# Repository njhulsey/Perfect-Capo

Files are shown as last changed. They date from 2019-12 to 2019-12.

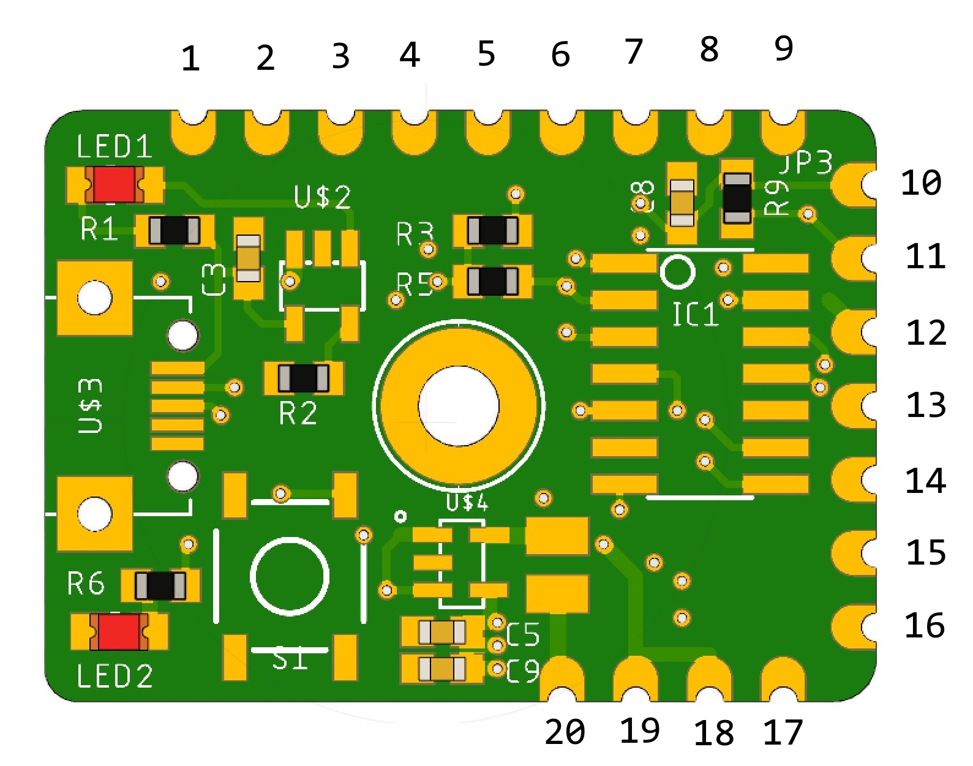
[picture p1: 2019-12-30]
Photos/pinout.jpg

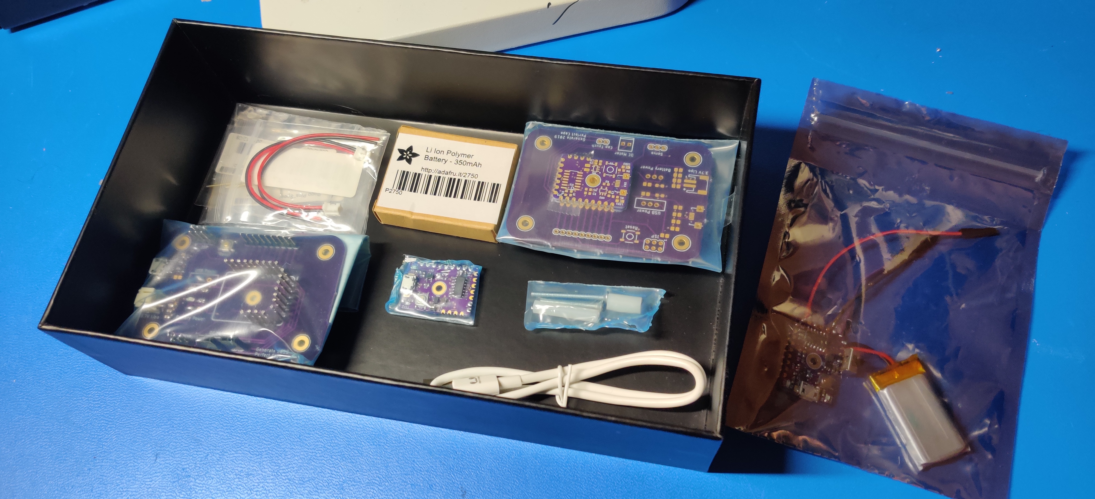
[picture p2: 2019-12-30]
Photos/IMG_20191204_212945.jpg

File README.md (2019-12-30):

# Perfect-Capo
The electrical system of perfect-capo is capable of unclenching the clamp mechanism via capacitive touch. The board uses an ATtiny84 MCU for basic logic and control. It is capable of driving the speed and direction of a DC Motor via an H-bridge. The pins along the edge of the PCB are for external connections to be soldered on (such as Motor, Capacitive touch, Battery, Switch). The entire system is powered by a 3.7v LiPo Battery which is buck-boosted to 5v for better motor performance. A Micro-USB connector is present for programming and battery charging. The MCU uses a bootloader to simulate USB for simple hardware implementation. It is also able to charge the LiPo via the MCP73831 IC. Many additional pinouts are available for easy hackability and ease of use.

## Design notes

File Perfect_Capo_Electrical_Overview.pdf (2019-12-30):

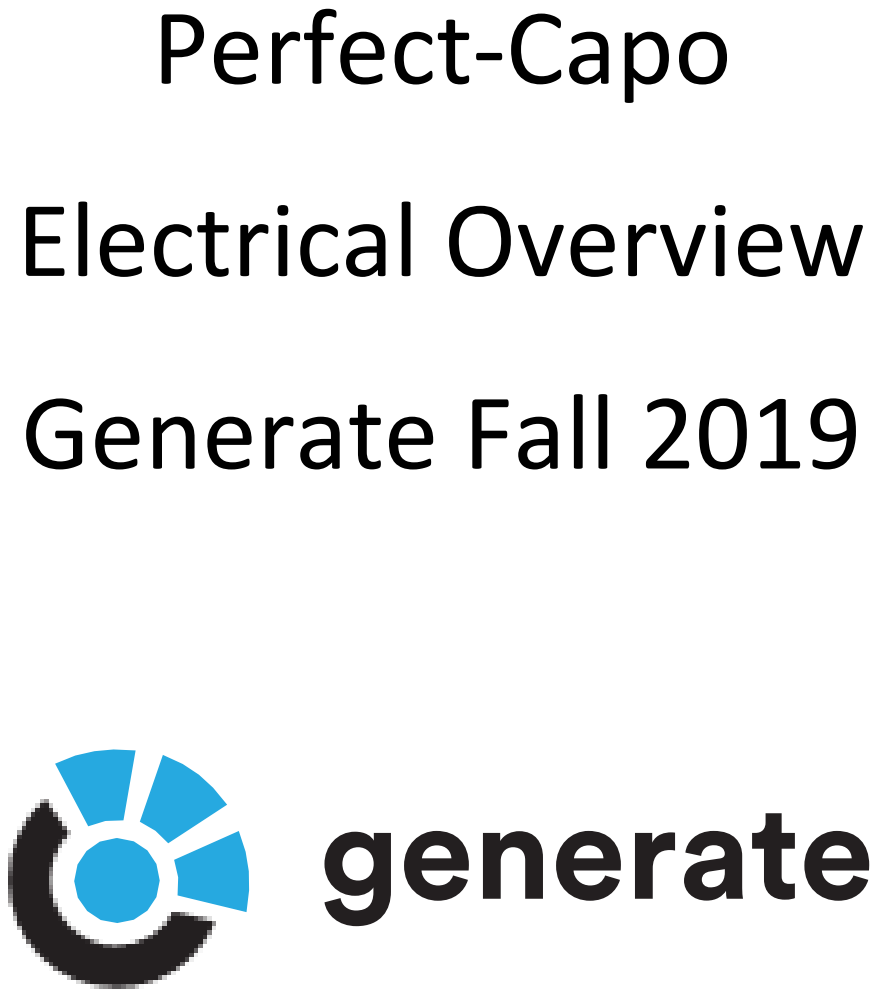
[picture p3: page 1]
Perfect-Capo; Electrical Overview; Generate Fall 2019

## Overview:

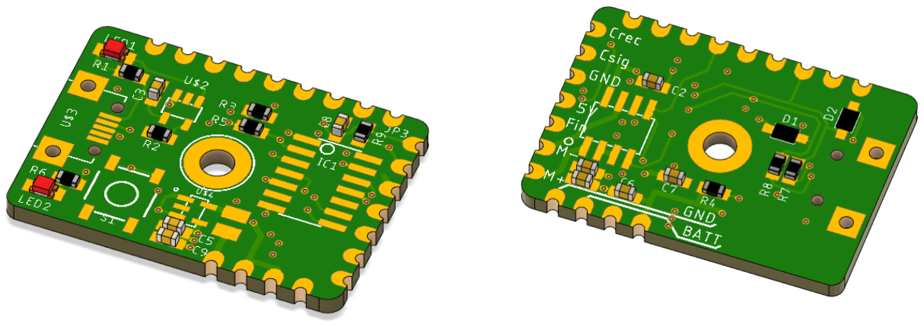
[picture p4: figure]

The electrical system of perfect-capo is capable of unclenching the clamp mechanism via capacitive touch. The board uses an ATtiny84 MCU for basic logic and control. It is capable of driving the speed and direction of a DC Motor via an H-bridge. The pins along the edge of the PCB are for external connections to be soldered on (such as Motor, Capacitive touch, Battery, Switch). The entire system is powered by a 3.7v LiPo Battery which is buck-boosted to 5v for better motor performance. A Micro-USB connector is present for programming and battery charging. The MCU uses a bootloader to simulate USB for simple hardware implementation. It is also able to charge the LiPo via the MCP73831 IC. Many additional pinouts are available for easy hackability and ease of use.

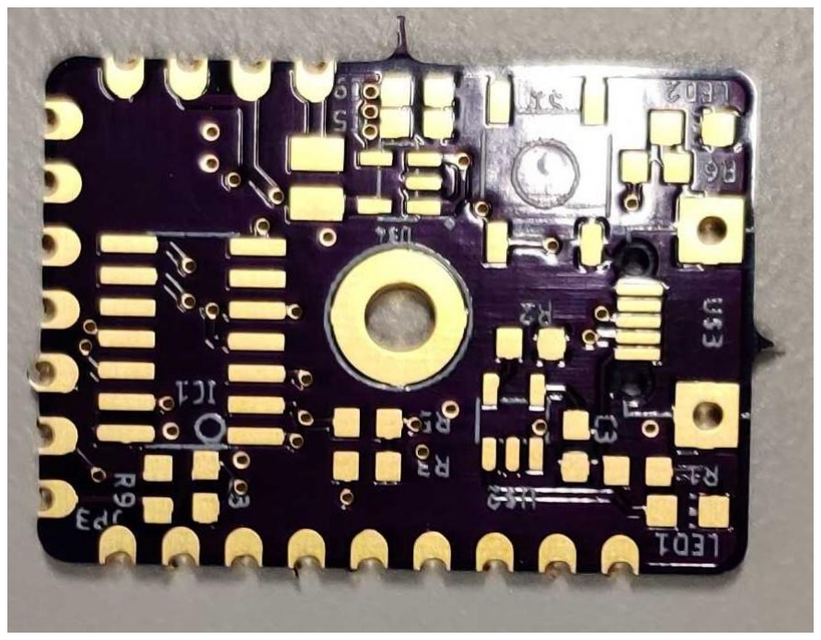
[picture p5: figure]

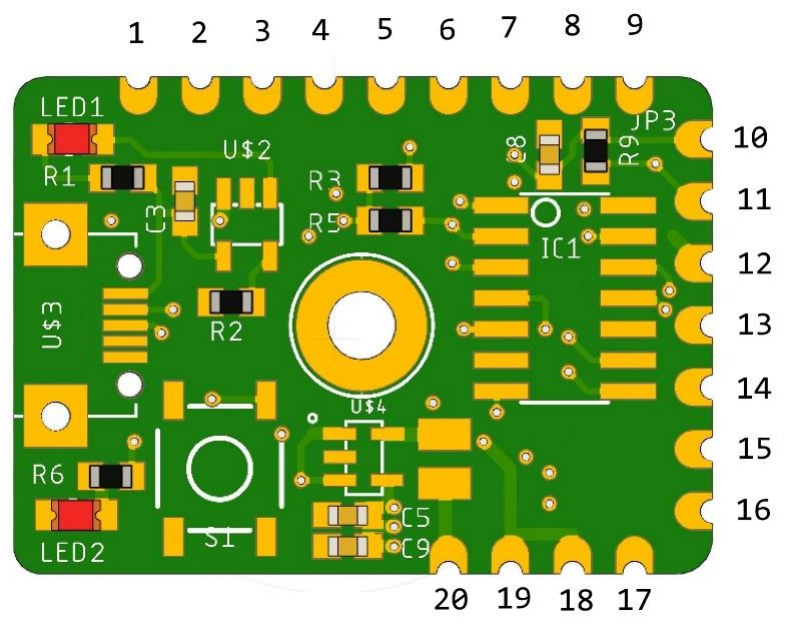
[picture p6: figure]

Pin | Function | Pin_Ref
1 | Miso | 5
2 | Reset | Reset(11)
3 | D- | 10
4 | D+ | 9
5 | GND | GND
6 | Rin | 6
7 | Fin | 8
8 | SCK | 4
9 | 5V | 5V
10 | Cap_Rec | 2
11 | Cap_Sig | 1
12 | GND | GND
13 | 5V | 5v
14 | Fin | 8
15 | M- | N/A
16 | M+ | N/A
17 | Bat_GND | N/A
18 | V_Bat | N/A
19 | Switch1 | N/A
20 | Switch2 | N/A

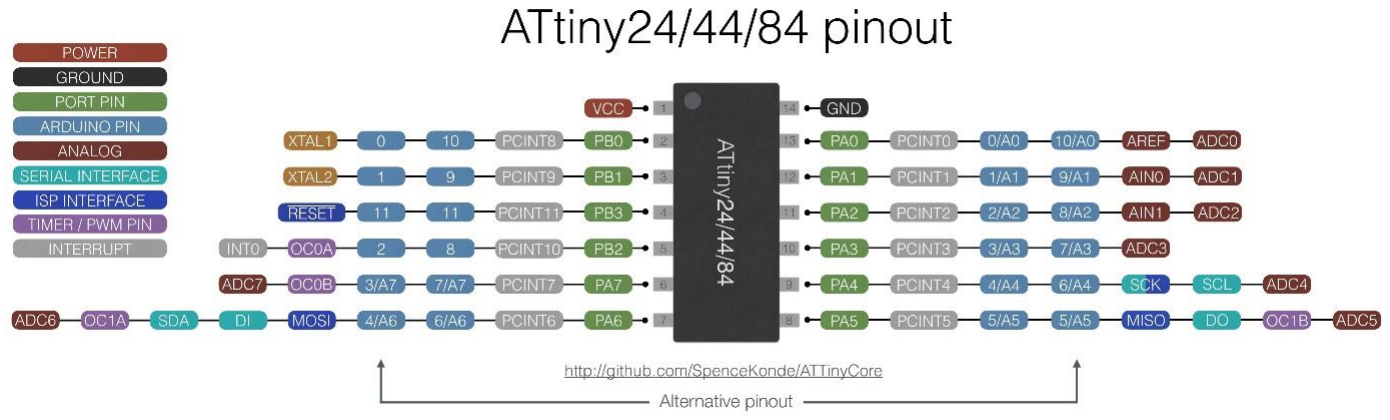
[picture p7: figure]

## Hardware:

The hardware overview will focus on each crucial portion of the schematic. Explaining how it works, its limits, why its there, and additional information.

Sections:

- ATtiny 84
- 5V Booster
- H-Bridge
- LiPo Charger

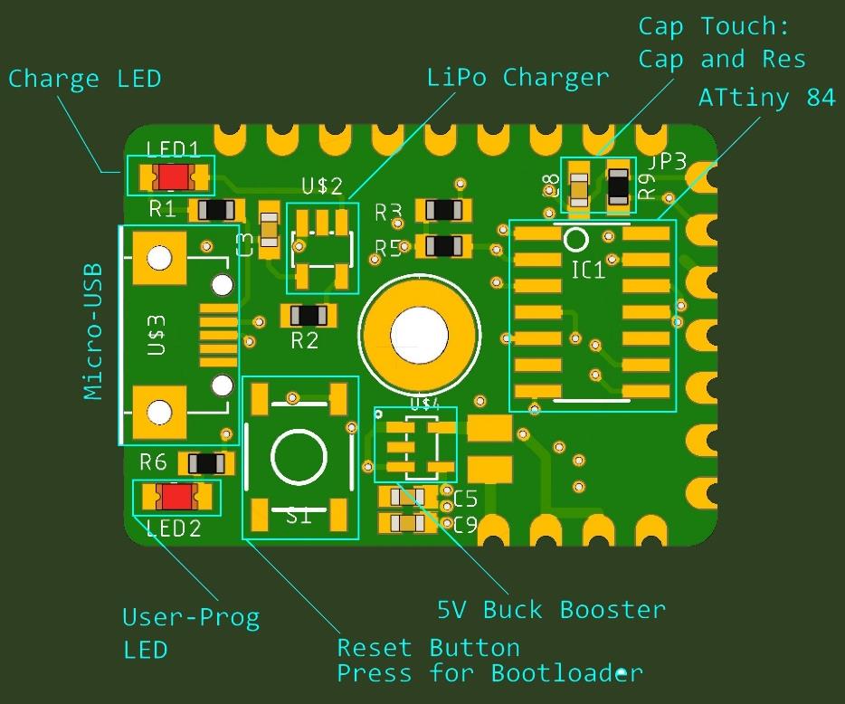
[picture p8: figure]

Physical Board Layout

## ATtiny 84:

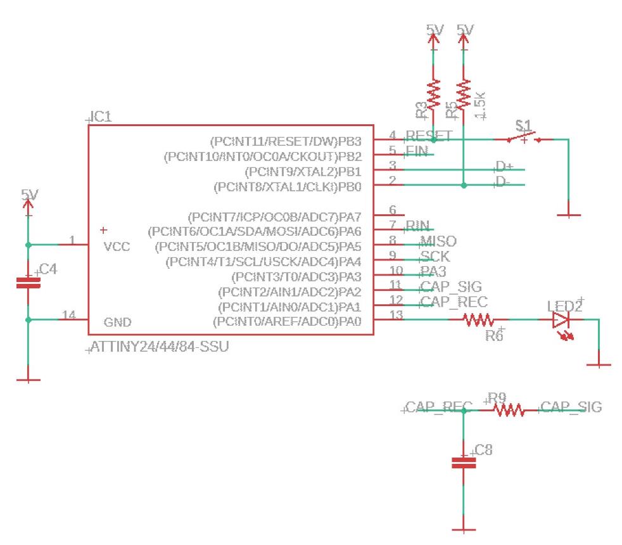
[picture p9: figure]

The ATtiny84 holds the core functionality and logic for the device. It engages the motor as it detects the capacitive touch. There is a debug LED used for testing purposes or additional indication. The Reset button is required to force the ATtiny84 into it’s bootloader. Once in the bootloader the device will wait for 10 seconds before running the user defined program. During those 10 seconds the user defined program can be rewritten with IDE and Micro-USB. C8 and R9 are used for setting the RC constant for capacitive touch (more info in software section). As usual there is a 100nF capacitor near the 5V and GND pin to reduce noise.

Additional Resources:

- Bootloader How-To:
- https://learn.sparkfun.com/tutorials/how-to-install-an-attiny-bootloader-with-virtualusb/all (https://learn.sparkfun.com/tutorials/how-to-install-an-attiny-bootloader-with-virtual-usb/all)
- Capacitive Touch:
- https://playground.arduino.cc/Main/CapacitiveSensor/
- ATtiny 84:
- https://www.digikey.com/product-detail/en/microchip-technology/ATTINY84A-SSUR/ATTINY84A-SSURCT-ND/2774136 (https://www.digikey.com/product-detail/en/microchip-technology/ATTINY84A-SSUR/ATTINY84A-SSURCT-ND/2774136)

## 5V Buck-Booster:

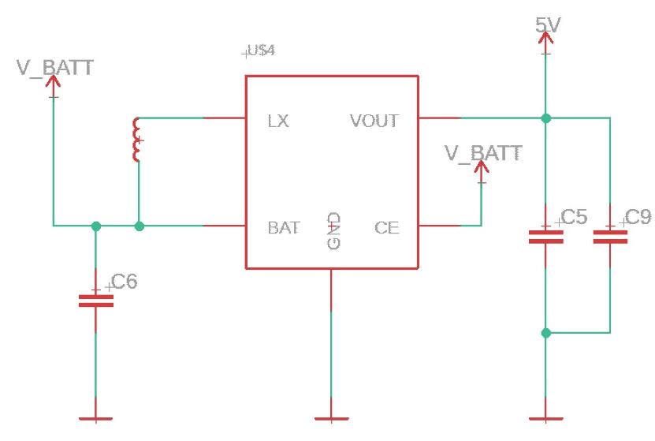
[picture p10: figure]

The XC9141B50 IC is capable of boosting the LiPo battery and providing 5V and 800mA to the entire system. It uses a 4.7uH inductor with a switching frequency of 1Mhz. It provides just enough to power the DC motor. Ideally it should be able to supply more current since the max torque current draw of the DC Motor is exactly 800mA. Also, more capacitance is needed. Additional capacitors were soldered on after fabrication. The capacitors used here were rated: 0603 10V 10uF.

Additional Resources:

- Buck Booster IC:
- https://www.digikey.com/product-detail/en/torex-semiconductor-ltd/XC9141B50CMR-G/893-1369-1-ND/6148753 (https://www.digikey.com/product-detail/en/torex-semiconductor-ltd/XC9141B50CMR-G/893-1369-1-ND/6148753)
- Inductor:
- https://www.digikey.com/product-detail/en/w-rth-elektronik/74405024047/732-10778-1-ND/6598212 (https://www.digikey.com/product-detail/en/w-rth-elektronik/74405024047/732-10778-1-ND/6598212)

## H-Bridge:

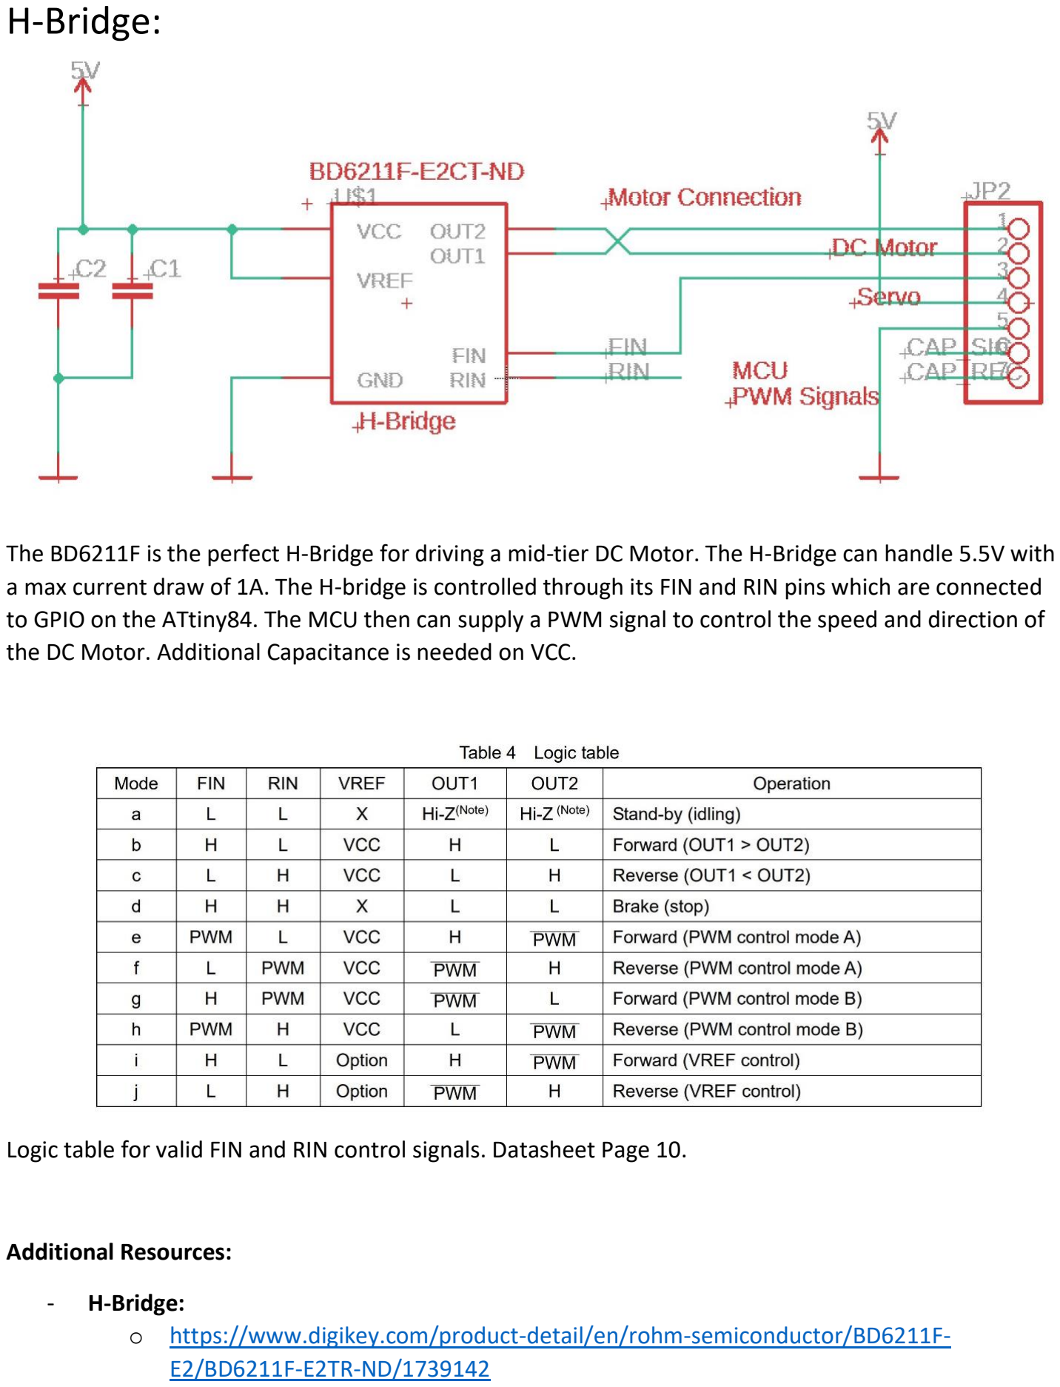
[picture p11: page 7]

The BD6211F is the perfect H-Bridge for driving a mid-tier DC Motor. The H-Bridge can handle 5.5V with a max current draw of 1A. The H-bridge is controlled through its FIN and RIN pins which are connected to GPIO on the ATtiny84. The MCU then can supply a PWM signal to control the speed and direction of the DC Motor. Additional Capacitance is needed on VCC.

Logic table for valid FIN and RIN control signals. Datasheet Page 10.

Additional Resources:

- H-Bridge:
- https://www.digikey.com/product-detail/en/rohm-semiconductor/BD6211F-E2/BD6211F-E2TR-ND/1739142 (https://www.digikey.com/product-detail/en/rohm-semiconductor/BD6211F-E2/BD6211F-E2TR-ND/1739142)

## Lipo-Charger:

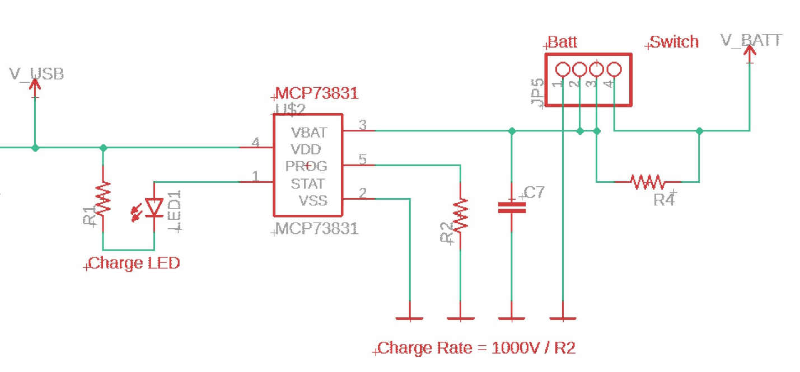
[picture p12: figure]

The MCP73831 is an amazingly convenient single cell 4.2v LiPo charger. It’s easy to implement and operate. A single resistor sets the charge rate (which should not be greater than the capacity of the LiPo). The LED indicates the charge status. The STAT pin will be grounded while charging and high when done charging. The direction of the LED will indicate either state.

It should be noted that the photo above also includes pinouts (JP5:3 JP5:4) for a switch (which is also R4). This could be used as a power switch for the perfect-capo unit.

Additional Resources:

- LiPo Charger IC:
- https://www.digikey.com/product-detail/en/MCP73831T-2ACI%2fOT/MCP73831T-2ACI%2fOTCT-ND/1979802 (https://www.digikey.com/product-detail/en/MCP73831T-2ACI%2fOT/MCP73831T-2ACI%2fOTCT-ND/1979802)

## Development Board:

Since the Perfect-Capo PCB is rather small, a development board was created to help with initial prototyping and ease of interfacing. Another use for the development board could be for mass production testing. The board has pogo-pins which allow for quick and easy temporary connection. The dev board can perform initial programming and testing before continuing through production.

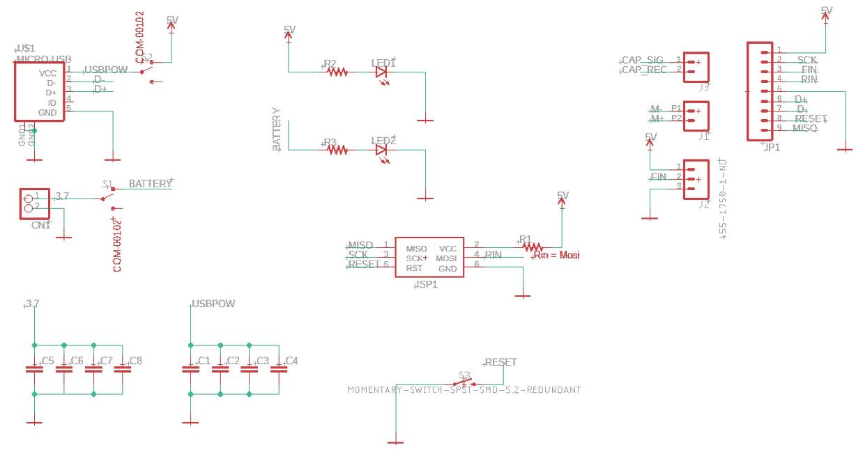
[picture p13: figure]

The Development Board provides a connector for every feature of the perfect-capo PCB. The PCB has power switches for Battery and USB which allows for power selection. Pin headers are primarily used for external connections. There is also ISP Programming pins for initial bootloader flashing. Silkscreen also provides information, labelling each connector.

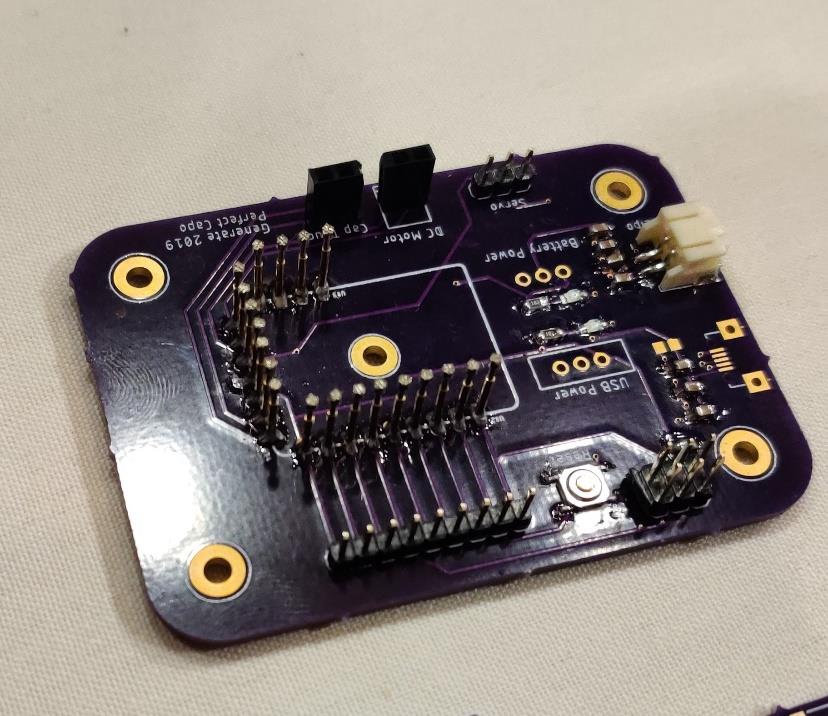
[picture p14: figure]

## What’s in The Box?

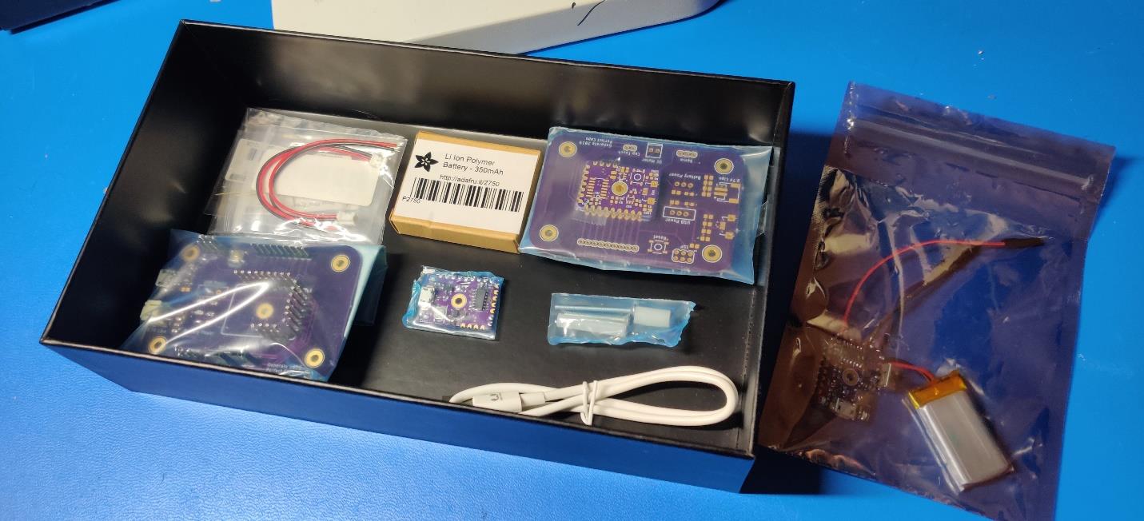
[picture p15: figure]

The box handed off to the client will contain the entire electrical prototype as well as spare electrical components crucial to development.

Contents:

- Capo electrical prototype
- 1x PCBA Dev board and capo controller
- Spare Battery
- Micro-Usb cable
- Spare Hardware
- Spare Battery connectors and pogo pins
- 2x PCB Dev board and capo controller

## BOM

Part Number | Description | Price | Quantity
CDS0D323-T08L | USB TVS Diode | $0.73 | 2
TL3342F160QG | Reset Button! | $0.70 | 1
ATTINY84A-SSUR | MCU | $0.84 | 1
MCP73831T-2ACI/OT | USB Charger | $0.58 | 1
10118194-0001LF | Micro USB | $0.43 | 1
1528-1858-ND | Battery 350mAh | $6.95 | 1
587-3258-1-ND | 0603 10uF 10V Cap | $0.19 | 35
XC9141B50CMR-G | IC REG BOOST 5V 800MA SOT25 | $1.27 | 1
732-10778-1-ND | FIXED IND 4.7UH 1A 270 MOHM MAX | $0.63 | 1
Various Resistors not shown

## Additional Photos:

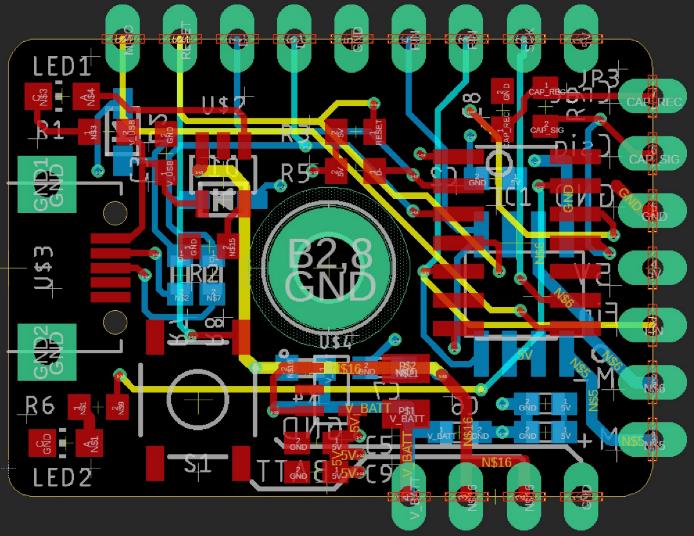
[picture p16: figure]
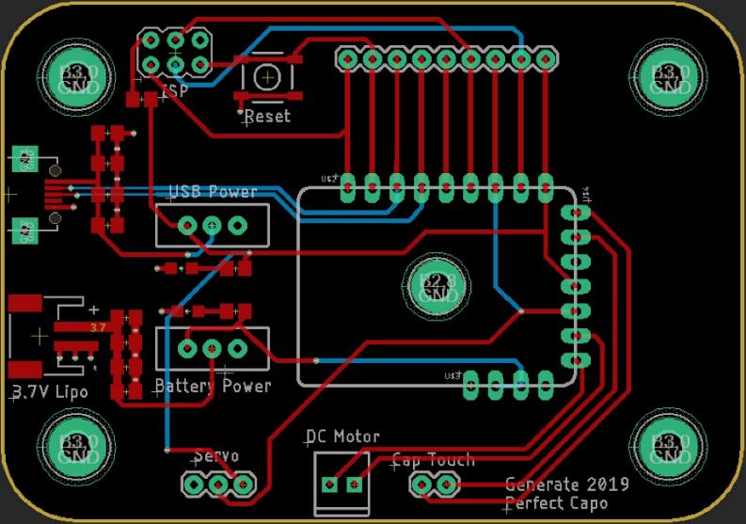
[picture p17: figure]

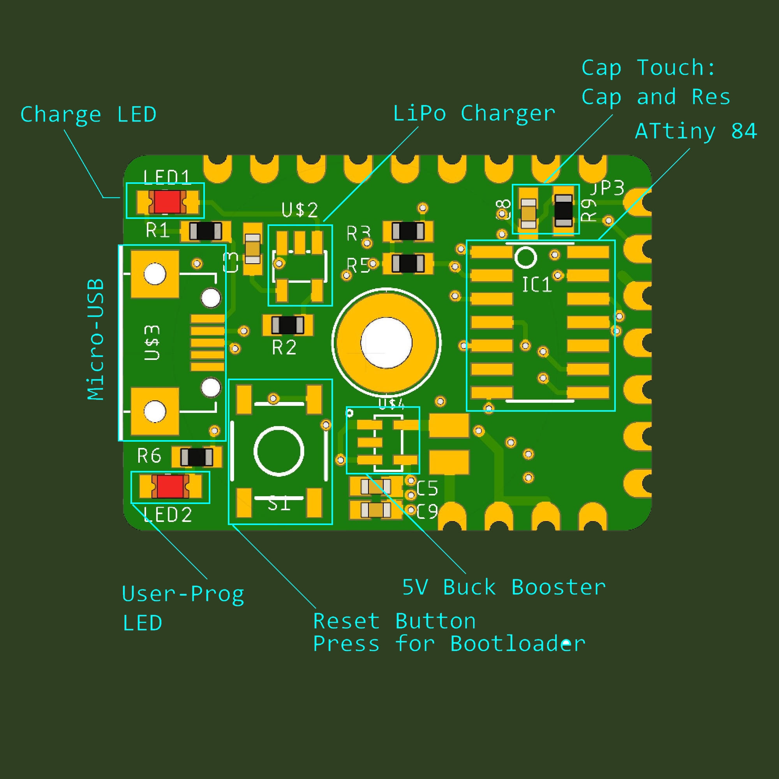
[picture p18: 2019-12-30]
Photos/HardWare.jpg

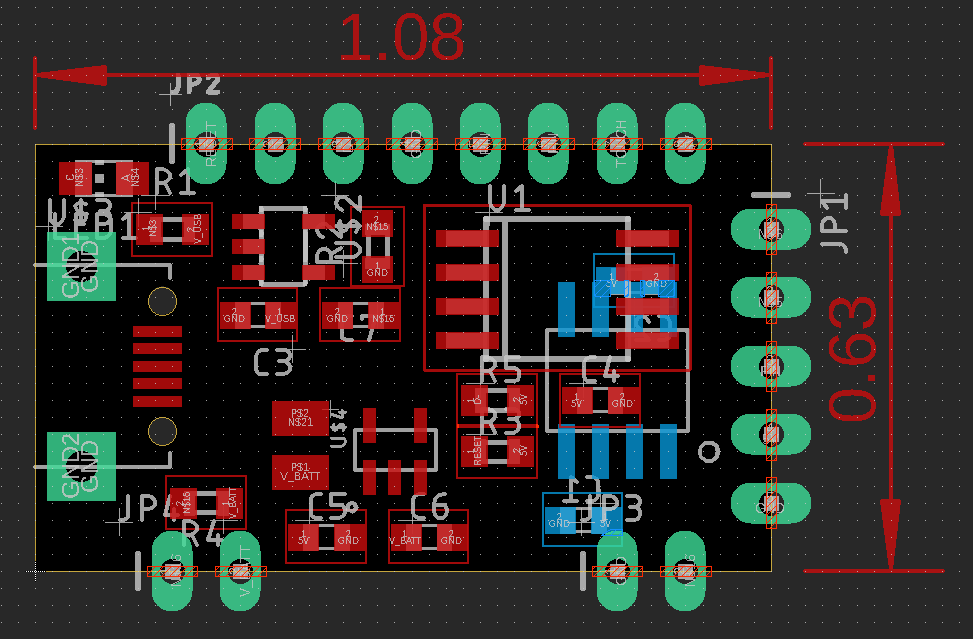
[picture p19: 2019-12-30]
Eagle_Files/Initial_Board.PNG

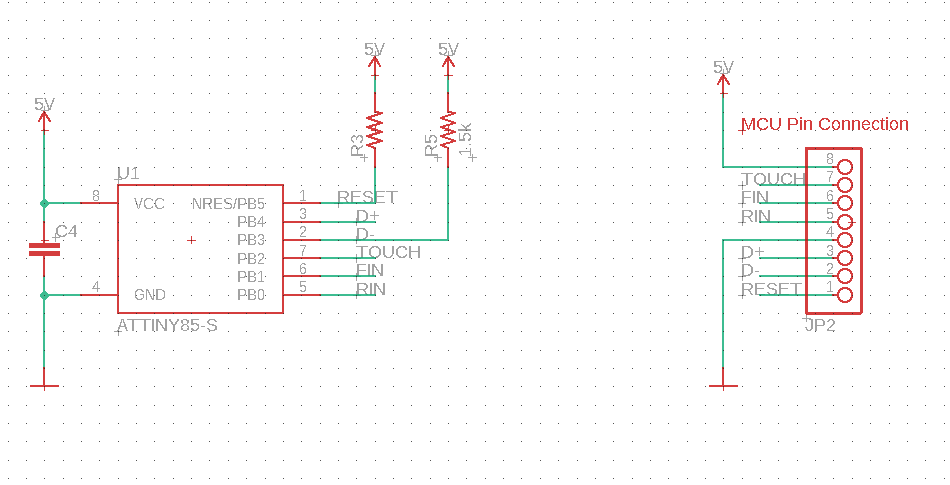
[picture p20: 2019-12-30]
Eagle_Files/MCU-Pins.PNG

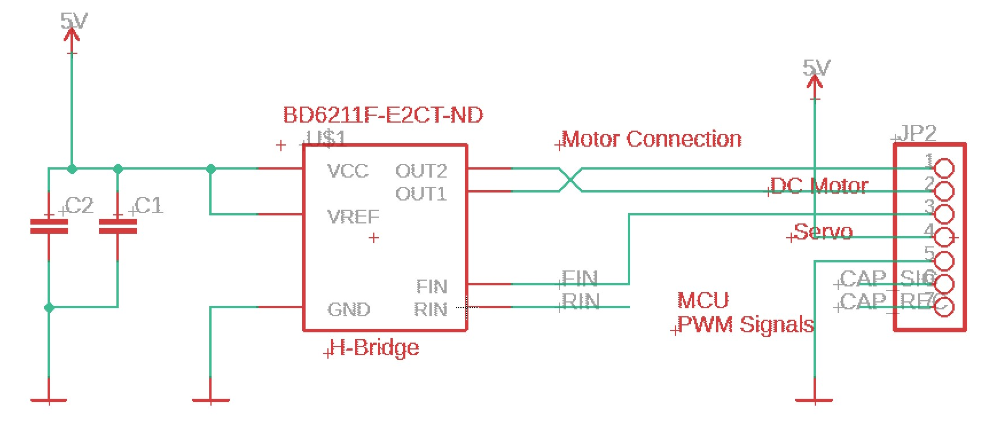
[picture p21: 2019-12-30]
Eagle_Files/H-Bridge.PNG

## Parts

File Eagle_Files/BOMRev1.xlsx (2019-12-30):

Part Number | Description | Reference | Price | Quantity | Manufacturer | Link
CDS0D323-T08L | USB TVS Diode |  | $0.73 | 2 | Bourns | https://www.mouser.com/ProductDetail/Bourns/CDSOD323-T08L
TL3342F160QG | Reset Button! |  | $0.70 | 1 |  | https://www.digikey.com/product-detail/en/e-switch/TL3342F160QG-TR/EG2531CT-ND/379004
ATTINY84A-SSUR‎ | MCU |  | $0.84 | 1 |  | https://www.digikey.com/product-detail/en/microchip-technology/ATTINY84A-SSUR/ATTINY84A-SSURCT-ND/2774136
MCP73831T-2ACI/OT‎ | USB Charger |  | $0.58 | 1 |  | https://www.digikey.com/product-detail/en/microchip-technology/MCP73831T-2ACI-OT/MCP73831T-2ACI-OTCT-ND/1979802
10118194-0001LF | Micro USB |  | $0.43 | 1 |  | https://www.digikey.com/product-detail/en/amphenol-icc-fci/10118194-0001LF/609-4618-1-ND/2785382
1528-1858-ND | Battery 350mAh |  | $6.95 | 1 |  | https://www.digikey.com/products/en?keywords=1528-1858-ND
587-3258-1-ND | 0603 10uF 10V Cap |  | $0.19 | 35 |  | https://www.digikey.com/products/en?keywords=587-3258-1-ND
XC9141B50CMR-G | IC REG BOOST 5V 800MA SOT25 |  | $1.27 | 1 |  | https://www.digikey.com/product-detail/en/torex-semiconductor-ltd/XC9141B50CMR-G/893-1369-1-ND/6148753
732-10778-1-ND | FIXED IND 4.7UH 1A 270 MOHM MAX |  | $0.63 | 1 |  | https://www.digikey.com/products/en?keywords=732-10778-1-ND

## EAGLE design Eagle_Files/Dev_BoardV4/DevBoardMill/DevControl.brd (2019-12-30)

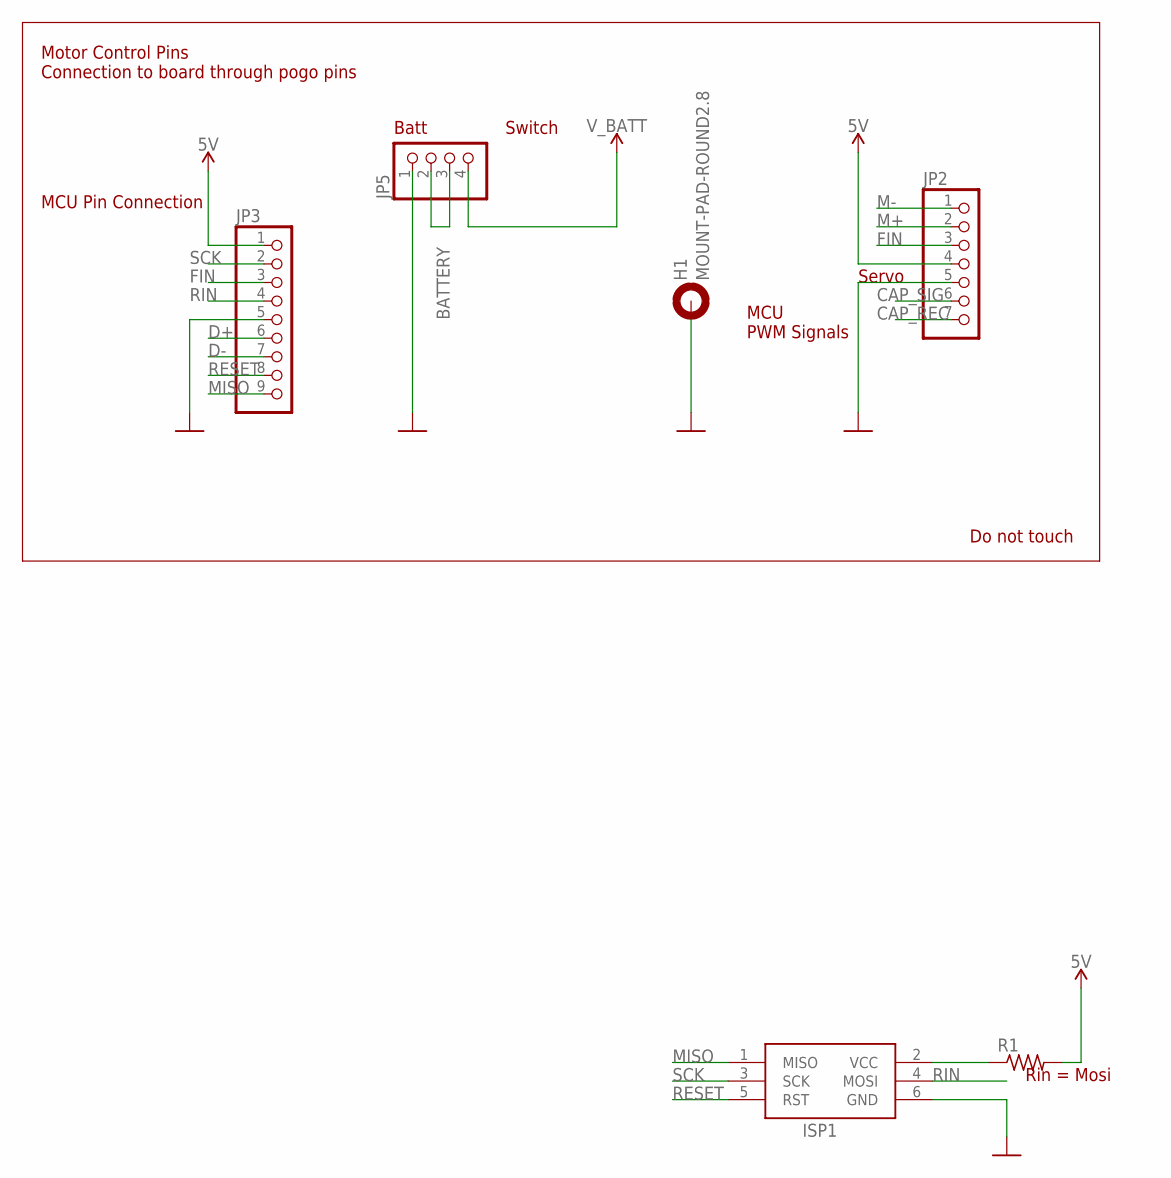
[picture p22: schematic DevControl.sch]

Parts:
H1: MOUNT-PAD-ROUND2.8; 2,8-PAD
ISP1: AVRISP-6; AVRISP
JP2: HEADER-1X7; 1X07_OVAL
JP3: HEADER-1X9; 1X09_OVAL
JP5: HEADER-1X4; 1X04_OVAL
R1: R-US_R0805; R0805

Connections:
5V: JP2.4, JP3.1, R1.2
BATTERY: JP5.2, JP5.3
CAP_REC: JP2.7
CAP_SIG: JP2.6
D+: JP3.6
D-: JP3.7
FIN: JP2.3, JP3.3
GND: H1.B2,8, ISP1.6 (GND), JP2.5, JP3.5, JP5.1
M+: JP2.2
M-: JP2.1
MISO: ISP1.1 (MISO), JP3.9
unnamed: ISP1.2 (VCC), R1.1
RESET: ISP1.5 (RST), JP3.8
RIN: ISP1.4 (MOSI), JP3.4
SCK: ISP1.3 (SCK), JP3.2
V_BATT: JP5.4

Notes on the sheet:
MCU PWM Signals
Batt
Switch
MCU Pin Connection
Servo
Motor Control Pins Connection to board through pogo pins
Do not touch
Rin = Mosi

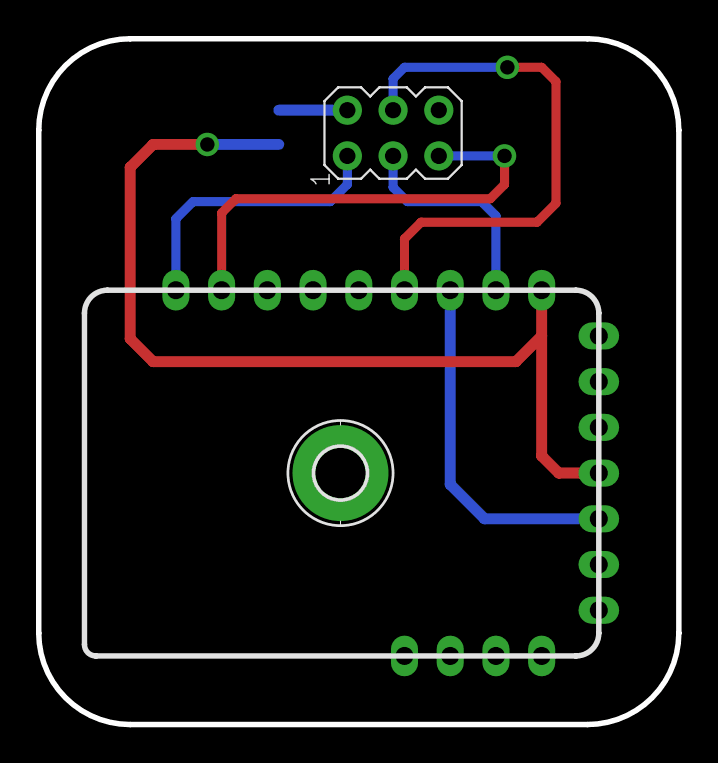
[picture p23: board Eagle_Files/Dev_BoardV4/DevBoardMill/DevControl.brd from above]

Board: 2 copper layers, 35.6 x 38.1 mm, 6 parts (1 on the bottom side), 9 nets.

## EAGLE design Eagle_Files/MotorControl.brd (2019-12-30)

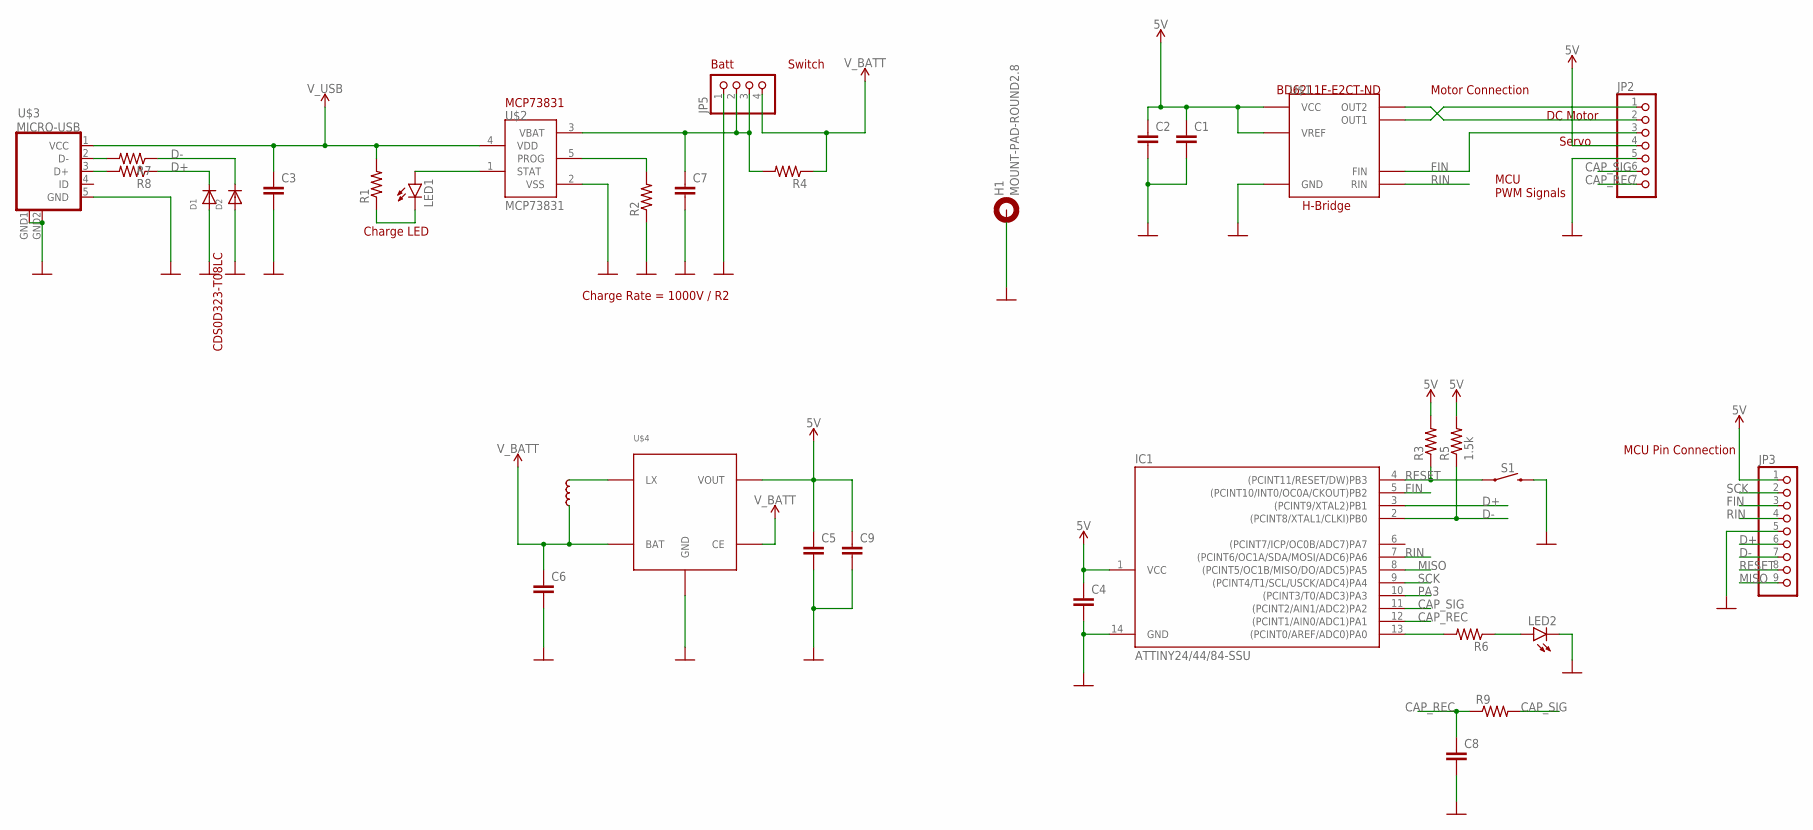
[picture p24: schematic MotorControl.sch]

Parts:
C1, C2, C3, C4, C5, C6, C7, C8, C9: C-EUC0603; C0603
D1, D2: DIODESOD-323; SOD-323
H1: MOUNT-PAD-ROUND2.8; 2,8-PAD
IC1: ATTINY24/44/84-SSU; SOIC14
JP2: HEADER-1X7; 1X07_OVAL
JP3: HEADER-1X9; 1X09_OVAL
JP5: HEADER-1X4; 1X04_OVAL
LED1, LED2: LEDCHIP-LED0805; CHIP-LED0805
R1, R2, R3, R4, R6, R7, R8, R9: R-US_R0603; R0603
R5: 1.5k; R0603
S1: MOMENTARY-SWITCH-SPST-SMD-5.2MM; TACTILE_SWITCH_SMD_5.2MM
U$1: H-BRIDGE-BD6210F; 8-SOP
U$2: MCP73831; SOT23-5L
U$3: MICRO-USB
U$4: XC9141B50C; SOT-25
U$5: INDUCTOR; SMD_INDUCTOR

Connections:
5V: C1.1, C2.1, C4.1, C5.1, C9.1, IC1.1 (VCC), JP2.4, JP3.1, R3.2, R5.2, U$1.P$2 (VCC), U$1.P$3 (VCC), U$1.P$6 (VREF), U$4.P$4 (VOUT)
CAP_REC: C8.1, IC1.12 ((PCINT1/AIN0/ADC1)PA1), JP2.7, R9.1
CAP_SIG: IC1.11 ((PCINT2/AIN1/ADC2)PA2), JP2.6, R9.2
D+: D1.C, IC1.3 ((PCINT9/XTAL2)PB1), JP3.6, R8.1
D-: D2.C, IC1.2 ((PCINT8/XTAL1/CLKI)PB0), JP3.7, R5.1, R7.1
FIN: IC1.5 ((PCINT10/INT0/OC0A/CKOUT)PB2), JP2.3, JP3.3, U$1.P$4 (FIN)
GND: C1.2, C2.2, C3.2, C4.2, C5.2, C6.2, C7.2, C8.2, C9.2, D1.A, D2.A, H1.B2,8, IC1.14 (GND), JP2.5, JP3.5, JP5.1, LED2.C, R2.1, S1.3 (2), U$1.P$8 (GND), U$2.2 (VSS), U$3.5 (GND), U$3.GND1 (GND), U$3.GND2 (GND), U$4.P$2 (GND)
MISO: IC1.8 ((PCINT5/OC1B/MISO/DO/ADC5)PA5), JP3.9
unnamed: LED2.A, R6.1
unnamed: R7.2, U$3.2 (D-)
unnamed: LED1.C, R1.1
unnamed: LED1.A, U$2.1 (STAT)
unnamed: JP2.1, U$1.P$1 (OUT1)
unnamed: JP2.2, U$1.P$7 (OUT2)
unnamed: R8.2, U$3.3 (D+)
unnamed: IC1.13 ((PCINT0/AREF/ADC0)PA0), R6.2
unnamed: R2.2, U$2.5 (PROG)
unnamed: C7.1, JP5.2, JP5.3, R4.2, U$2.3 (VBAT)
unnamed: U$4.P$5 (LX), U$5.P$2
PA3: IC1.10 ((PCINT3/T0/ADC3)PA3)
RESET: IC1.4 ((PCINT11/RESET/DW)PB3), JP3.8, R3.1, S1.1
RIN: IC1.7 ((PCINT6/OC1A/SDA/MOSI/ADC6)PA6), JP3.4, U$1.P$5 (RIN)
SCK: IC1.9 ((PCINT4/T1/SCL/USCK/ADC4)PA4), JP3.2
V_BATT: C6.1, JP5.4, R4.1, U$4.P$1 (CE), U$4.P$3 (BAT), U$5.P$1
V_USB: C3.1, R1.2, U$2.4 (VDD), U$3.1 (VCC)

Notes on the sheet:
MCU PWM Signals
Motor Connection
BD6211F-E2CT-ND
MCP73831
Batt
Switch
Charge LED
Charge Rate = 1000V / R2
H-Bridge
MCU Pin Connection
DC Motor
Servo
CDS0D323-T08LC

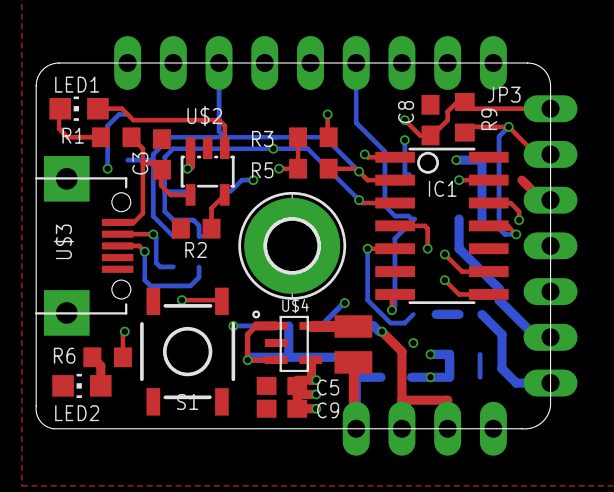
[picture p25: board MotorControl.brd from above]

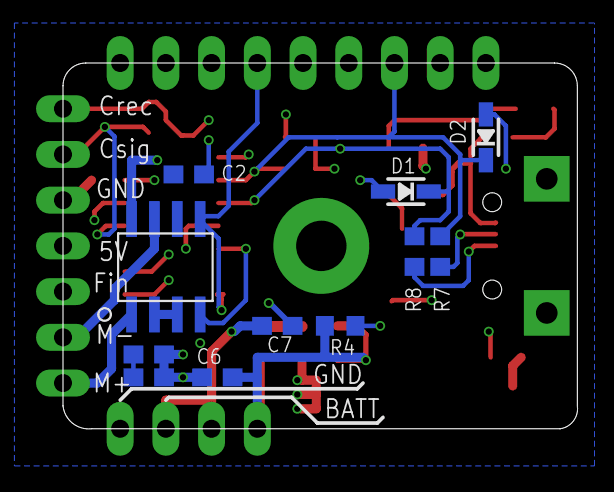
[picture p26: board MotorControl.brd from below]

Board: 4 copper layers, 28.6 x 20.3 mm, 33 parts (11 on the bottom side), 24 nets.

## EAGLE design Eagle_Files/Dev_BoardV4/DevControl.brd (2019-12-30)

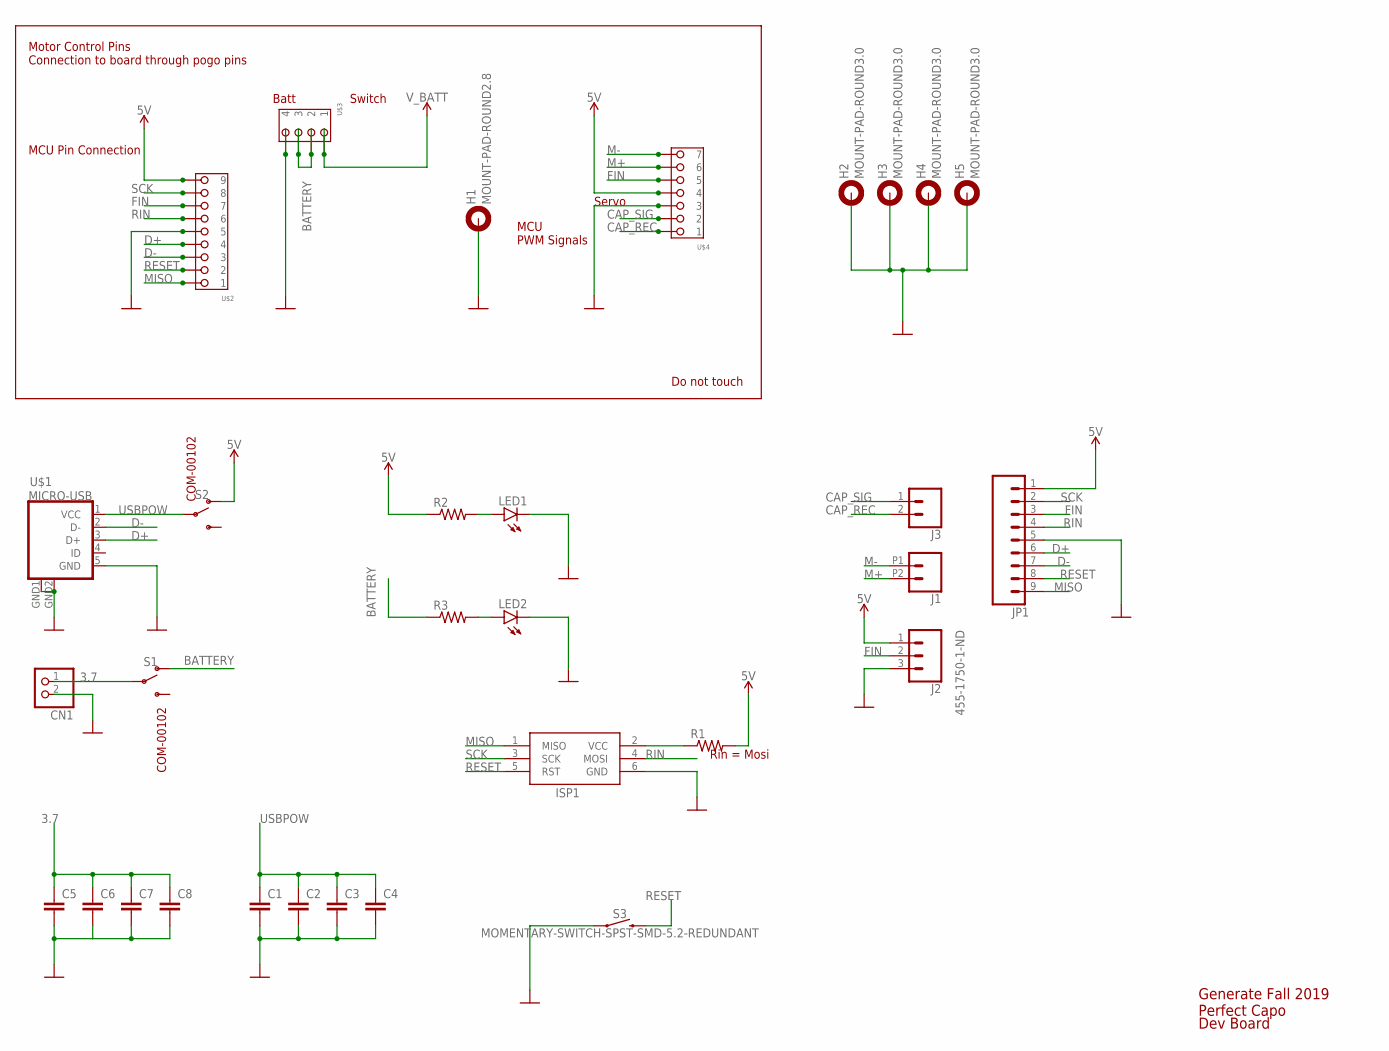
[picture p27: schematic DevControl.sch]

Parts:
C1, C2, C3, C4, C5, C6, C7, C8: C-EUC0805; C0805
CN1: JST_2PIN-SMT-RA; JST-PH-2-SMT-RA
H1: MOUNT-PAD-ROUND2.8; 2,8-PAD
H2, H3, H4, H5: MOUNT-PAD-ROUND3.0; 3,0-PAD
ISP1: AVRISP-6; AVRISP
J1: CONN_022.54MM_SCREWTERM; 1X02_2.54_SCREWTERM
J2: 455-1750-1-ND; 1X03
J3: CONN_02; 1X02
JP1: CONN_09; 1X09
LED1, LED2: LEDCHIPLED_0805; CHIPLED_0805
R1, R2, R3: R-US_R0805; R0805
S1, S2: SWITCH-SPDT-PTH-11.6X4.0MM; SWITCH_SPDT_PTH_11.6X4.0MM
S3: MOMENTARY-SWITCH-SPST-SMD-5.2-REDUNDANT; TACTILE_SWITCH_SMD_5.2MM
U$1: MICRO-USB
U$2: POGO-1X9
U$3: POGO-1X4
U$4: POGO-1X7

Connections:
3.7: C5.1, C6.1, C7.1, C8.1, CN1.1 (2), S1.2
5V: J2.1, JP1.1, R1.2, R2.1, S2.1 (O), U$2.P$9 (9), U$4.P$4 (4)
BATTERY: R3.1, S1.1 (O), U$3.P$2 (2), U$3.P$3 (3)
CAP_REC: J3.2, U$4.P$1 (1)
CAP_SIG: J3.1, U$4.P$2 (2)
D+: JP1.6, U$1.3 (D+), U$2.P$4 (4)
D-: JP1.7, U$1.2 (D-), U$2.P$3 (3)
FIN: J2.2, JP1.3, U$2.P$7 (7), U$4.P$5 (5)
GND: C1.2, C2.2, C3.2, C4.2, C5.2, C6.2, C7.2, C8.2, CN1.2 (1), H1.B2,8, H2.B3,0, H3.B3,0, H4.B3,0, H5.B3,0, ISP1.6 (GND), J2.3, JP1.5, LED1.C, LED2.C, S3.1, S3.2 (1), U$1.5 (GND), U$1.GND1 (GND), U$1.GND2 (GND), U$2.P$5 (5), U$3.P$4 (4), U$4.P$3 (3)
M+: J1.P2 (2), U$4.P$6 (6)
M-: J1.P1 (1), U$4.P$7 (7)
MISO: ISP1.1 (MISO), JP1.9, U$2.P$1 (1)
unnamed: ISP1.2 (VCC), R1.1
unnamed: LED1.A, R2.2
unnamed: LED2.A, R3.2
RESET: ISP1.5 (RST), JP1.8, S3.3 (2), S3.4 (2), U$2.P$2 (2)
RIN: ISP1.4 (MOSI), JP1.4, U$2.P$6 (6)
SCK: ISP1.3 (SCK), JP1.2, U$2.P$8 (8)
USBPOW: C1.1, C2.1, C3.1, C4.1, S2.2, U$1.1 (VCC)
V_BATT: U$3.P$1 (1)

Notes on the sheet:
MCU PWM Signals
Batt
Switch
MCU Pin Connection
Servo
Motor Control Pins Connection to board through pogo pins
Do not touch
Rin = Mosi
Generate Fall 2019 Perfect Capo
Dev Board
COM-00102

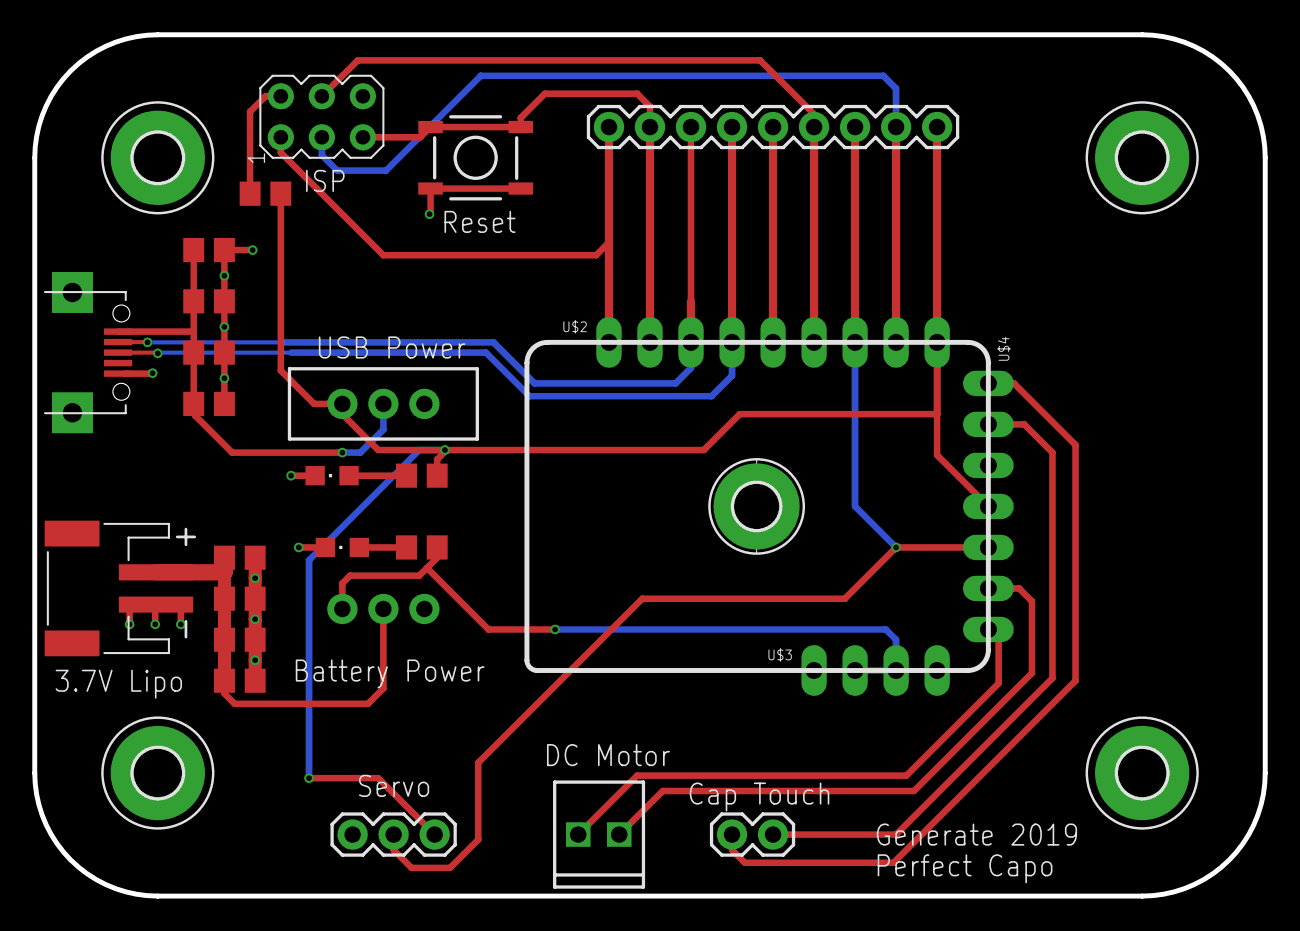
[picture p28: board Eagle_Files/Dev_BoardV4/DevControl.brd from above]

Board: 2 copper layers, 76.2 x 53.3 mm, 31 parts (1 on the bottom side), 19 nets.

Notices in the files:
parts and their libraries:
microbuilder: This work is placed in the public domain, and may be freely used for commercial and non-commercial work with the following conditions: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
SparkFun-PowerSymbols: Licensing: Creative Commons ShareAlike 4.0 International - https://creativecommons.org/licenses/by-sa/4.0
